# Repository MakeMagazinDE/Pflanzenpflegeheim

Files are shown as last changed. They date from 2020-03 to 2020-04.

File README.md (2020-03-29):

GitHub Logo

Maker Media GmbH
*** 

# Pflanzenpflegeheim
Pflanzenpflegeheim

### Mittels Arduino, Sensoren, Pumpen, Heizung und Lüfter wird dieses Ikea-Gewächshaus zum Luxus-Pflanzenheim.

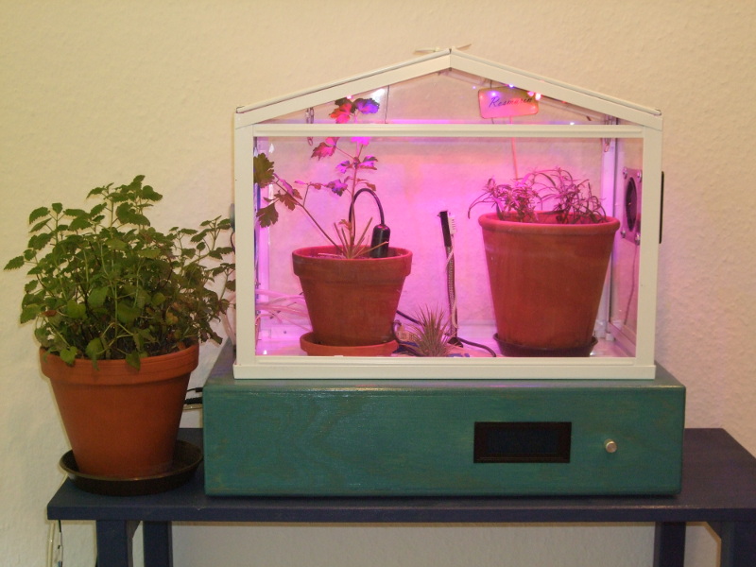
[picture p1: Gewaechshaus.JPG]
 

Den vollständigen Artikel mit der Bauanleitung gibt es in der Make-Ausgabe 2/2020 ab Seite 40 zu lesen.

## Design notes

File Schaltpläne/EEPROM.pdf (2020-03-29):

Adresse | Variable | Byte | Tag bzw. Kanal
0 | Temp an | low | Mo
1 | Temp an | high
2 | Temp an | low | Di
3 | Temp an | high
4 | Temp an | low | Mi
5 | Temp an | high
6 | Temp an | low | Do
7 | Temp an | high
8 | Temp an | low | Fr
9 | Temp an | high
10 | Temp an | low | Sa
11 | Temp an | high
12 | Temp an | low | So
13 | Temp an | high
14 | Temp aus | low | Mo
15 | Temp aus | high
16 | Temp aus | low | Di
17 | Temp aus | high
18 | Temp aus | low | Mi
19 | Temp aus | high
20 | Temp aus | low | Do
21 | Temp aus | high
22 | Temp aus | low | Fr
23 | Temp aus | high
24 | Temp aus | low | Sa
25 | Temp aus | high
26 | Temp aus | low | So
27 | Temp aus | high
28 | Temp aktiv | low | Mo
29 | | high
30 | Temp aktiv | low | Di
31 | | high
32 | Temp aktiv | low | Mi
33 | | high
34 | Temp aktiv | low | Do
35 | | high
36 | Temp aktiv | low | Fr
37 | | high
38 | Temp aktiv | low | Sa
39 | | high
40 | Temp aktiv | low | So
41 | | high
42 | Licht an | low | Mo
43 | Licht an | high
44 | Licht an | low | Di
45 | Licht an | high
46 | Licht an | low | Mi
47 | Licht an | high
48 | Licht an | low | Do
49 | Licht an | high
50 | Licht an | low | Fr
51 | Licht an | high
52 | Licht an | low | Sa
53 | Licht an | high
54 | Licht an | low | So
55 | Licht an | high
56 | Licht aus | low | Mo
57 | Licht aus | high
58 | Licht aus | low | Di
59 | Licht aus | high
60 | Licht aus | low | Mi
61 | Licht aus | high
62 | Licht aus | low | Do
63 | Licht aus | high
64 | Licht aus | low | Fr
65 | Licht aus | high
66 | Licht aus | low | Sa
67 | Licht aus | high
68 | Licht aus | low | So
69 | Licht aus | high
70 | Licht aktiv | low | Mo
71 | | high
72 | Licht aktiv | low | Di
73 | | high
74 | Licht aktiv | low | Mi
75 | | high
76 | Licht aktiv | low | Do
77 | | high
78 | Licht aktiv | low | Fr
79 | | high
80 | Licht aktiv | low | Sa
81 | | high
82 | Licht aktiv | low | So
83 | | high
84 | Pumpe an | low | Mo
85 | Pumpe an | high
86 | Pumpe an | low | Di
87 | Pumpe an | high
88 | Pumpe an | low | Mi
89 | Pumpe an | high
90 | Pumpe an | low | Do
91 | Pumpe an | high
92 | Pumpe an | low | Fr
93 | Pumpe an | high
94 | Pumpe an | low | Sa
95 | Pumpe an | high
96 | Pumpe an | low | So
97 | Pumpe an | high
98 | Pumpe aus | low | Mo
99 | Pumpe aus | high
100 | Pumpe aus | low | Di
101 | Pumpe aus | high
102 | Pumpe aus | low | Mi
103 | Pumpe aus | high
104 | Pumpe aus | low | Do
105 | Pumpe aus | high
106 | Pumpe aus | low | Fr
107 | Pumpe aus | high
108 | Pumpe aus | low | Sa
109 | Pumpe aus | high
110 | Pumpe aus | low | So
111 | Pumpe aus | high
112 | Pumpe aktiv | low | Mo
113 | | high
114 | Pumpe aktiv | low | Di
115 | | high
116 | Pumpe aktiv | low | Mi
117 | | high
118 | Pumpe aktiv | low | Do
119 | | high
120 | Pumpe aktiv | low | Fr
121 | | high
122 | Pumpe aktiv | low | Sa
123 | | high
124 | Pumpe aktiv | low | So
125 | | high
126 | Blende an | low | Mo
127 | Blende an | high
128 | Blende an | low | Di
129 | Blende an | high
130 | Blende an | low | Mi
131 | Blende an | high
132 | Blende an | low | Do
133 | Blende an | high
134 | Blende an | low | Fr
135 | Blende an | high
136 | Blende an | low | Sa
137 | Blende an | high
138 | Blende an | low | So
139 | Blende an | high
140 | Blende aus | low | Mo
141 | Blende aus | high
142 | Blende aus | low | Di
143 | Blende aus | high
144 | Blende aus | low | Mi
145 | Blende aus | high
146 | Blende aus | low | Do
147 | Blende aus | high
148 | Blende aus | low | Fr
149 | Blende aus | high
150 | Blende aus | low | Sa
151 | Blende aus | high
152 | Blende aus | low | So
153 | Blende aus | high
154 | Blende aktiv | low | Mo
155 | | high
156 | Blende aktiv | low | Di
157 | | high
158 | Blende aktiv | low | Mi
159 | | high
160 | Blende aktiv | low | Do
161 | | high
162 | Blende aktiv | low | Fr
163 | | high
164 | Blende aktiv | low | Sa
165 | | high
166 | Blende aktiv | low | So
167 | | high
168 | Bodenfeuchtigkeit | low | 0
169 | | high
170 | Bodenfeuchtigkeit | low | 1
171 | | high
172 | Bodenfeuchtigkeit | low | 2
173 | | high
174 | Bodenfeuchtigkeit | low | 3
175 | | high
176 | Bodenfeuchtigkeit | low | 4
177 | | high
178 | Bodenfeuchtigkeit | low | 5
179 | | high
180 | Bodenfeuchtigkeit | low | 6
181 | | high
182 | Licht | low | -
183 | | high
184 | Luftfeuchtigkeit soll | low | -
185 | | high
186 | Temperatur innen soll | low | -
187 | | high

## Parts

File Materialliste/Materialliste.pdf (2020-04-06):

Für das Gewächshaus

1 IKEA Socker

1 Schrittmotor z.B. 28BYJ-48 (mit Treiber z.B. von Pollin)

1 Silikonschlauch ca. 2 m, 8x2 mm

1 Temperatur/Luftfeuchtigkeitssensor DHT22

1 Pflanzlicht z.B. tronisky LED-Pflanzlampe von Amazon

1 Stück Lochrasterplatte

Elektronikdraht

1-6 Bodenfeuchtigkeitssensor Truebner SMT50

1 SUB-D Stecker 25 polig

1-6 Platinensteckverbinder und Kupplungen 3-polig

4 Kabelbinder

4 Schrauben zur Montage des Lüfters

1 Lüfter 80x80 mm z.B. SUNON MagLev Motor

1 - 2 Heizfolien 12 V, je nach Fläche 1-2 Stück aus dem KFZ-Bedarf

2 Sperrholz Dicke 12 mm, 51 x 28 cm (Oben, Unten)

Für den Sockel

2 Sperrholz Dicke 12 mm, 28 x 9,6 cm (Links, Rechts)

2 Sperrholz Dicke 12 mm, 51 x 9,6 cm (Vorne, Hinten)

1 Arduino Mega

1 Echtzeituhr DS3231

2 Temperatur/Luftfeuchtigkeitssensor DHT22

1 8-fach MOSFET-Treiber Bausatz von Pollin

1 4-fach MOSFET-Treiber Bausatz von Pollin

1-6 12V-Magnetventile CJV23-C12A1 (auf Ebay zu finden)

1 Messingrohr 6 mm Durchmesser, etwa 30 cm

2 Lochrasterkarten

1 LC-Display JOY-IT Display 20x4 Zeichen blau I2C

1 Netzteil 24 V, 5A

2 Step-Down-Wandler LM 2596 (als fertige Platinen verfügbar)

1 Pumpe Reich Tauchpumpe easy 14L/min

1 Sub-D Adapter, 25-polig z.B. von Pollin

2 LED-Treiber Meanwell LDD-500L

2 DC-Hohlstecker mit Kupplung für Heizfolie und Pumpe

1 ULN2003 zusammen mit Schrittmotor z.B. von Pollin

1 Kupplung, zu Netzteil passend

1 Lichtsensor BH 1750

1 5L-Kanister

1 Relais 12 V, mindestens ein Umschalter

1 BD441

1 Widerstand 680 kΩ

2 Widerstände 1 MΩ

1 Widerstand 2,5 kΩ

1 Widerstand 1,5 kΩ

4 Widerstände 10 kΩ

1 Elektrolytkondensator 100 µF

2 Kondensatoren 100 nF

1 Operationsverstärker z.B. LM741

1 Diode 1N4148

Elektronikdraht

diverse Schaltlitzen

diverse Platinensteckverbinder und Kupplungen 2 - 8 polig (optional)

1 Gewindestange M3 zur Befestigung des Arduinos

12 Muttern M3 zur Befestigung des Arduinos

4 Unterlegscheiben M3 zur Befestigung des Arduinos

diverse Platinenschraubverbindungen 2 polig (optional)

1 Drehimpulsgeber mit Taster ALPS - STEC11B

1 Drehknopf zur Welle des Drehimpulsgebers passend

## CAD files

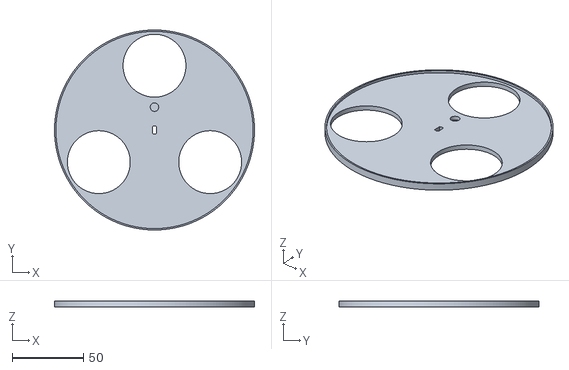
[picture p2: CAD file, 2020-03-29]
3D_Druck/Blende.stl
140.0 x 140.0 x 4.50

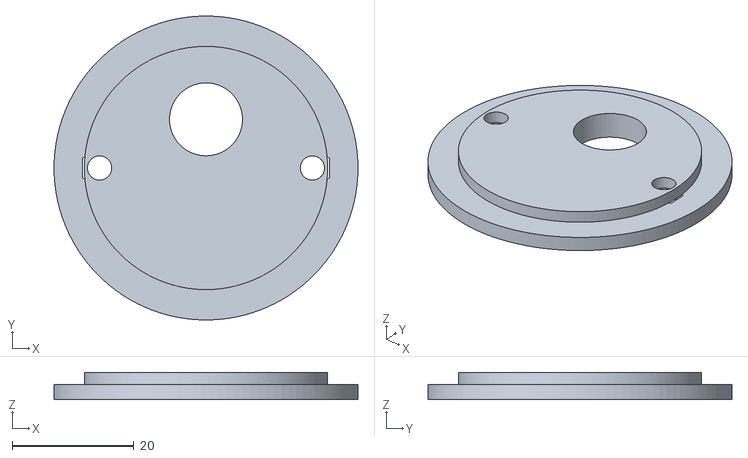
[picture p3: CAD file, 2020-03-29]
3D_Druck/Motorhalter_Blende.stl
50.0 x 50.0 x 4.50

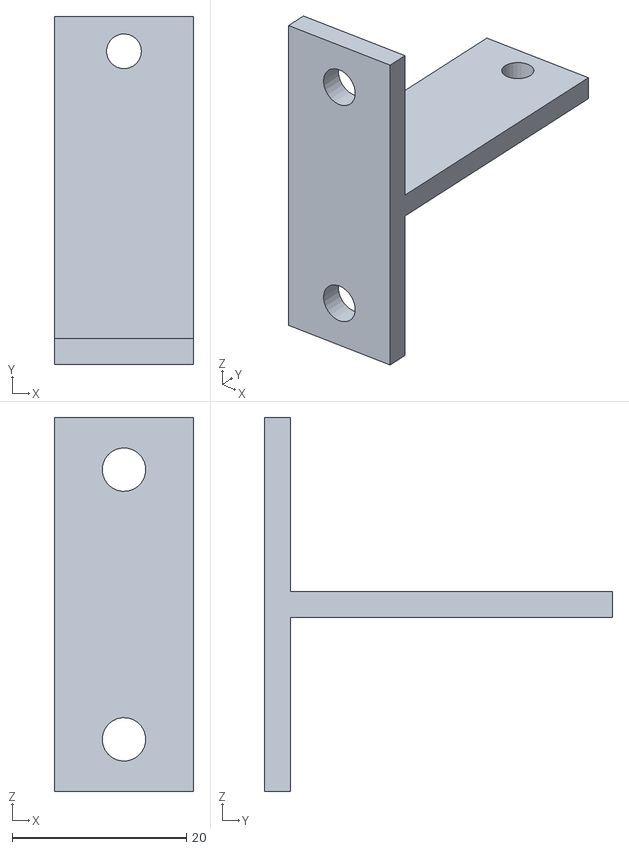
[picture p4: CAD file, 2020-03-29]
3D_Druck/Aufnahme_Tempsensor aussen.stl
16.0 x 40.0 x 43.0

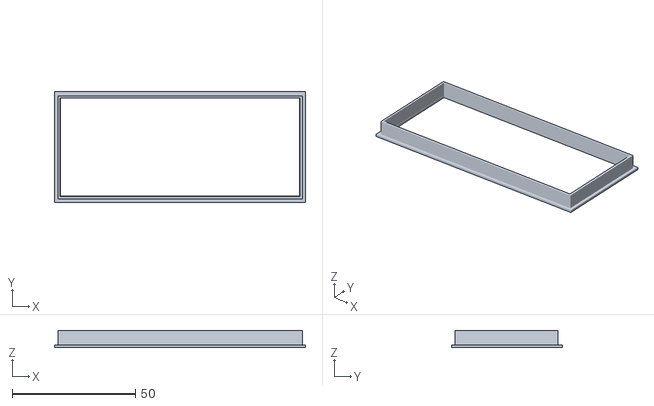
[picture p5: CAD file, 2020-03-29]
3D_Druck/Blende_Display.stl
102.0 x 45.0 x 7.00

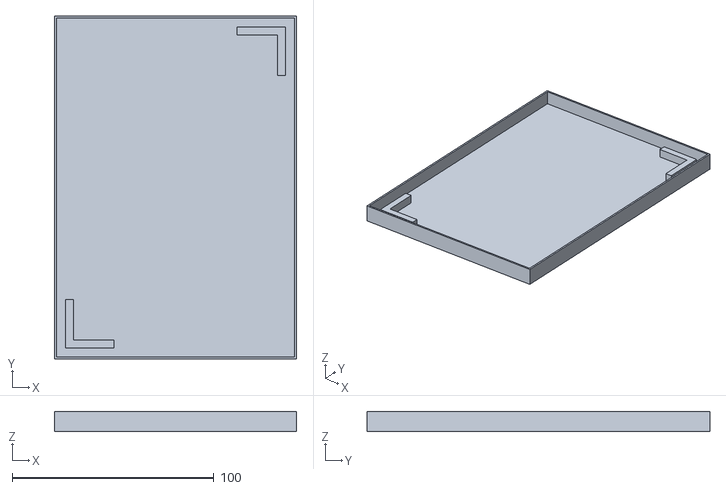
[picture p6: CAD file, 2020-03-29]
3D_Druck/Wanne_rev2.stl
120.0 x 170.0 x 10.0

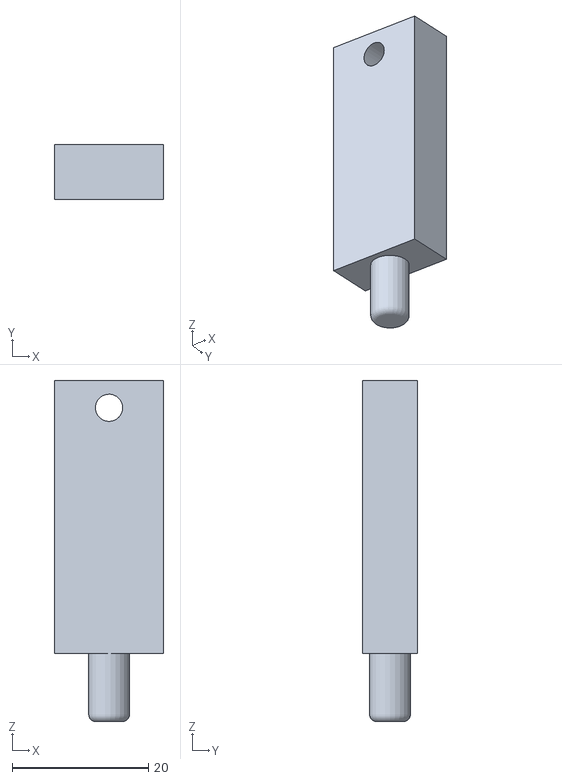
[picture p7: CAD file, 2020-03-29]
3D_Druck/Halterung_DHT22_Innen.stl
16.0 x 8.00 x 50.0

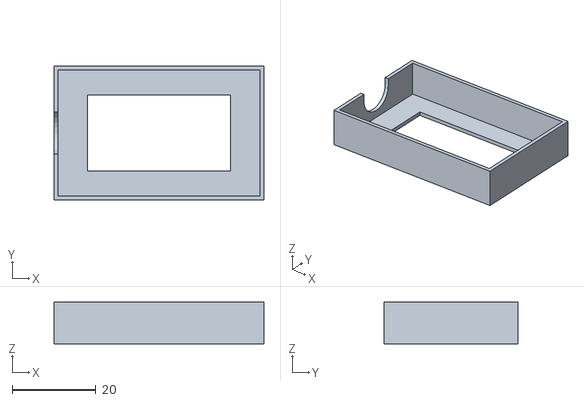
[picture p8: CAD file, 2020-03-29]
3D_Druck/Oberschale_Verteiler_Bodenfeuchtigkeit.stl
50.0 x 32.0 x 10.0

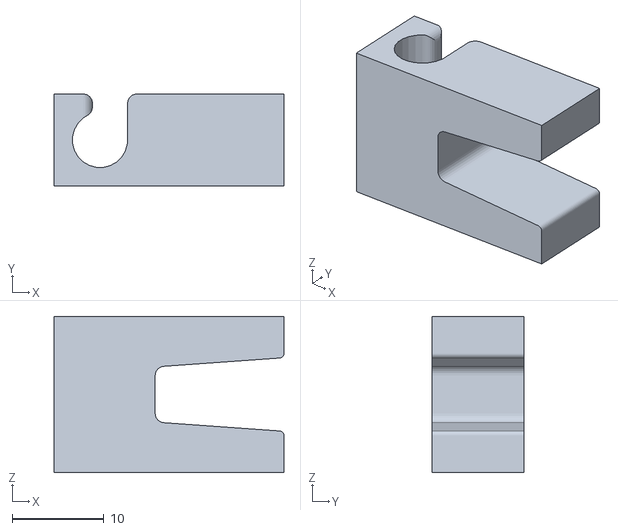
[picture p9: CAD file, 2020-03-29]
3D_Druck/Schlauchclip_fuer_Topf.stl
25.0 x 10.0 x 17.0

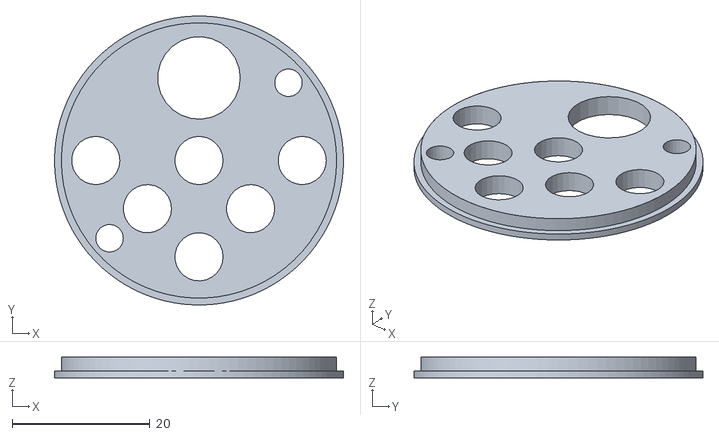
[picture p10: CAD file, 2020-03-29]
3D_Druck/Schlauchdurchfuehrung.stl
42.0 x 42.0 x 3.00

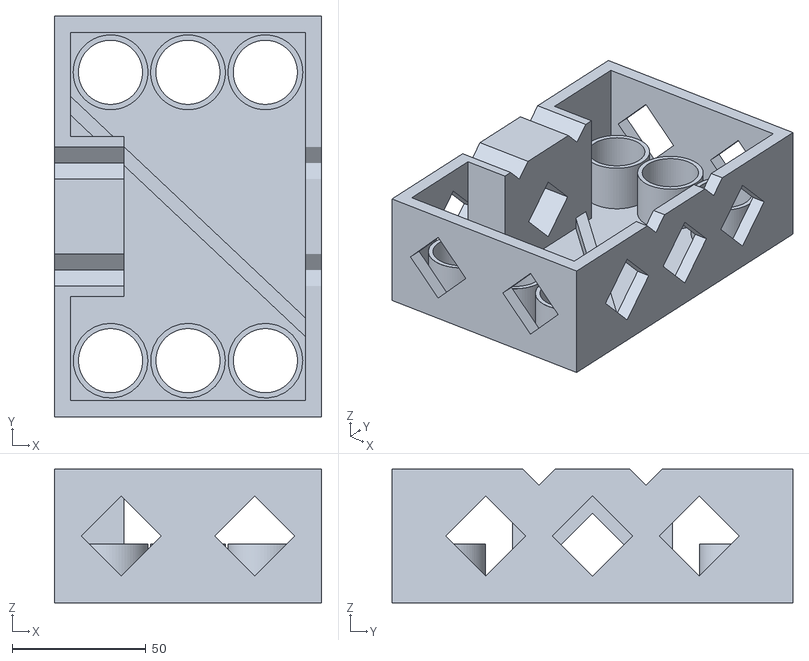
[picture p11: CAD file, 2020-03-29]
3D_Druck/Ventilblock_rev4.stl
100.0 x 150.0 x 50.0

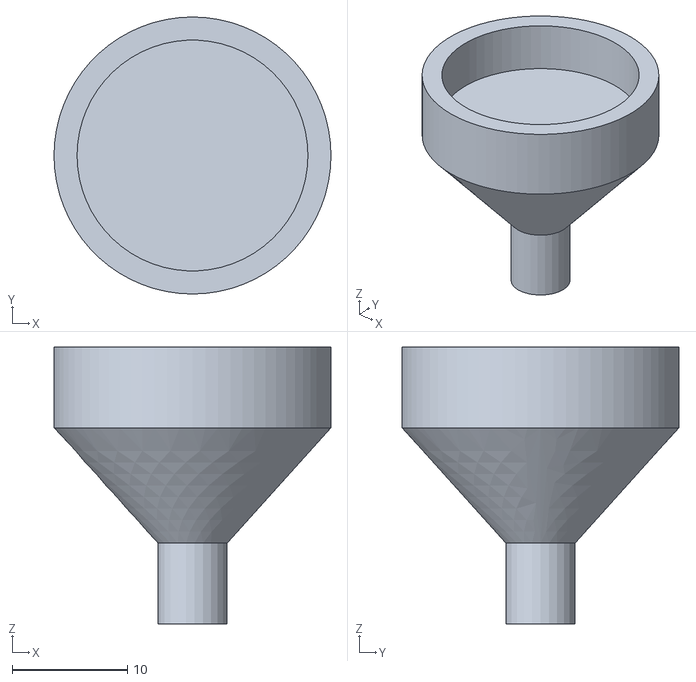
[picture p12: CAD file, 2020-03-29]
3D_Druck/Sockel_Halterung_DHT22_Innen.stl
24.0 x 24.0 x 24.0

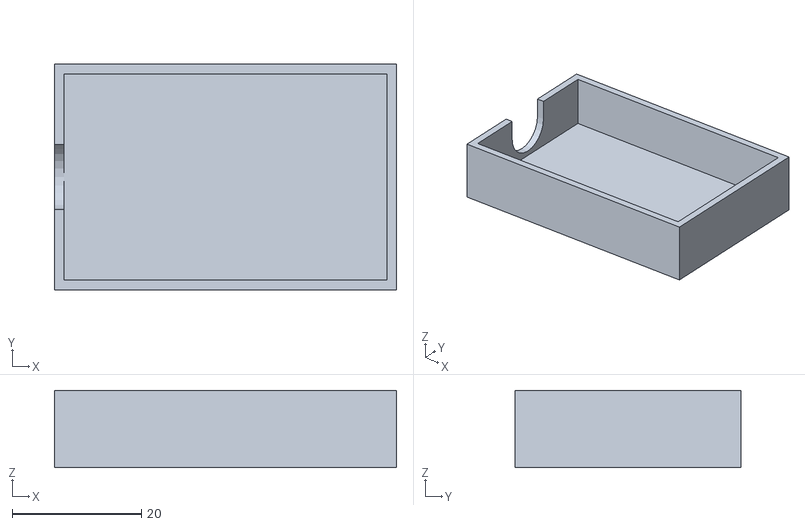
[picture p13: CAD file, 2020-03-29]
3D_Druck/Unterschale_Verteiler_Bodenfeuchtigkeit.stl
53.0 x 35.0 x 12.0

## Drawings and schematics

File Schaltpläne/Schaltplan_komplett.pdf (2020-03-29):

LM2596

IN-

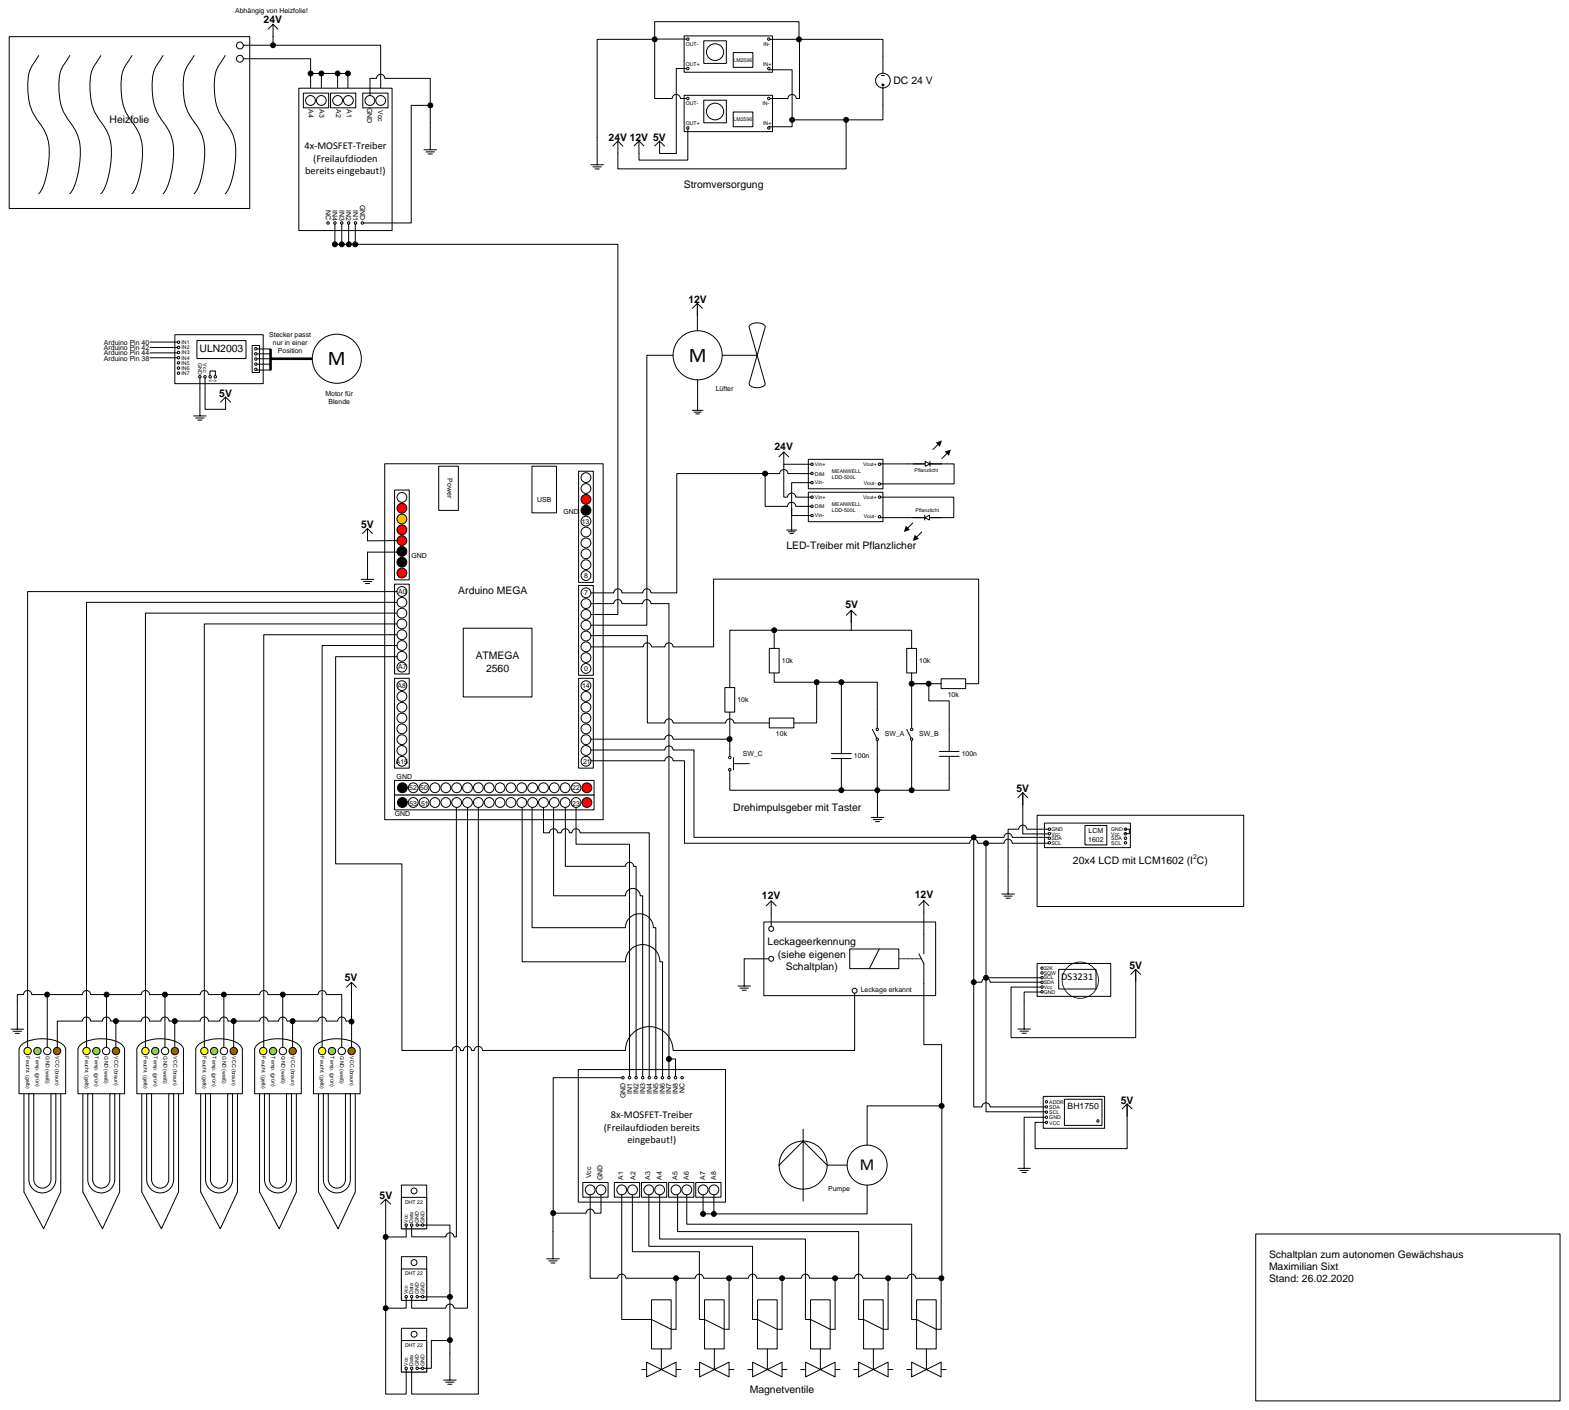
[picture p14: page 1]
Leckageerkennung; (siehe eigenen Schaltplan); Leckage erkannt 12V; Vcc GND; ATMEGA 2560 A0; GND; Power; USB; 20x4 LCD mit LCM1602 (I; C) GND Vcc SDA SCL; GND GND; Lüfter; IN+ OUT-; OUT+; Heizfolie; 24V Abhängig von Heizfolie!; GND Vcc GND; M Pumpe; Vin+; Vin-; DIM; Vout+; Vout- MEANWELL LDD-500L 24V; Pflanzlicht; ULN2003 GND Vcc <->; M Stecker passt nur in einer Position; Magnetventile; Stromversorgung; Arduino MEGA

4x-MOSFET-Treiber (Freilaufdioden bereits eingebaut!)

Motor für Blende 5V Arduino Pin 40 Arduino Pin 42 Arduino Pin 44 Arduino Pin 38

Vout- MEANWELL LDD-500L

LED-Treiber mit Pflanzlicher

Drehimpulsgeber mit Taster

SDA SCL LCM 1602

DS3231 GND Vcc SDA SCL SQW 32K

GND (weiß) VCC (braun) Temp. (grün) Feucht. (gelb)

ADDR SDA SCL GND VCC

8x-MOSFET-Treiber (Freilaufdioden bereits eingebaut!) GND

Vcc Data DHT 22

Schaltplan zum autonomen Gewächshaus Maximilian Sixt Stand: 26.02.2020

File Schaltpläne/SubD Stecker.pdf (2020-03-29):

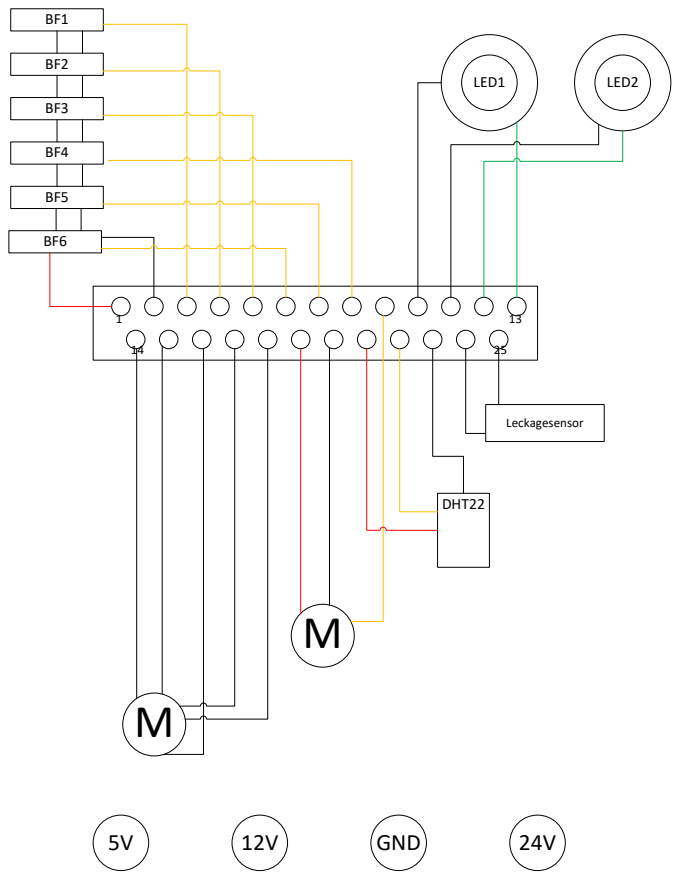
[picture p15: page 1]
DHT22; LED1; LED2; GND; Leckagesensor

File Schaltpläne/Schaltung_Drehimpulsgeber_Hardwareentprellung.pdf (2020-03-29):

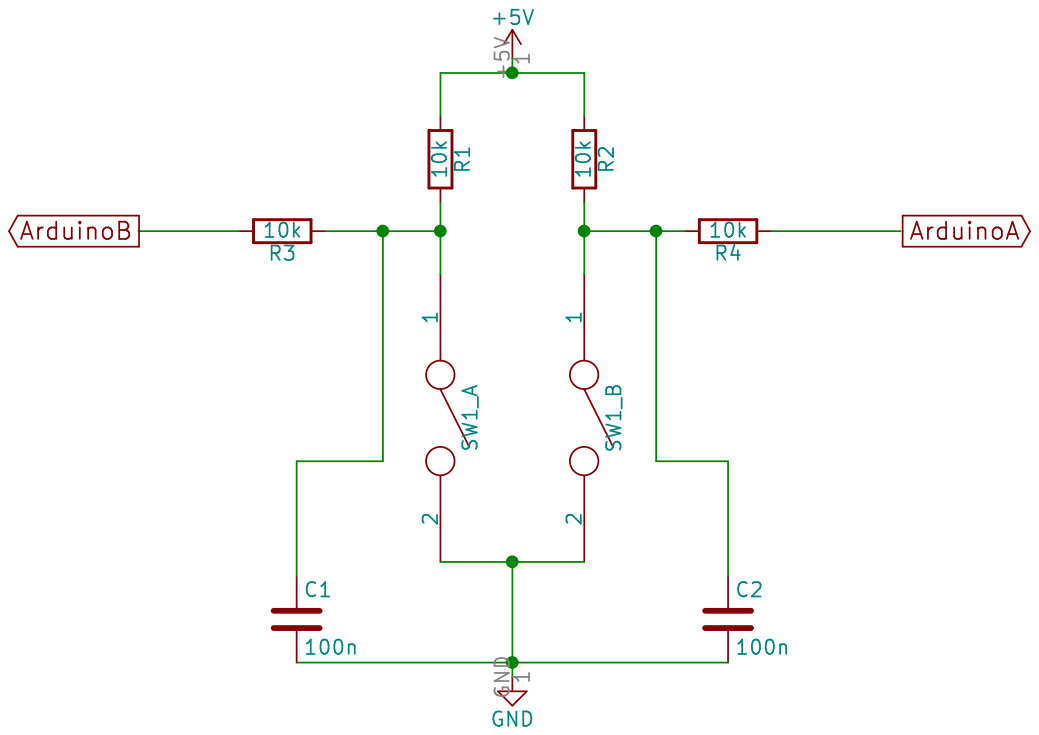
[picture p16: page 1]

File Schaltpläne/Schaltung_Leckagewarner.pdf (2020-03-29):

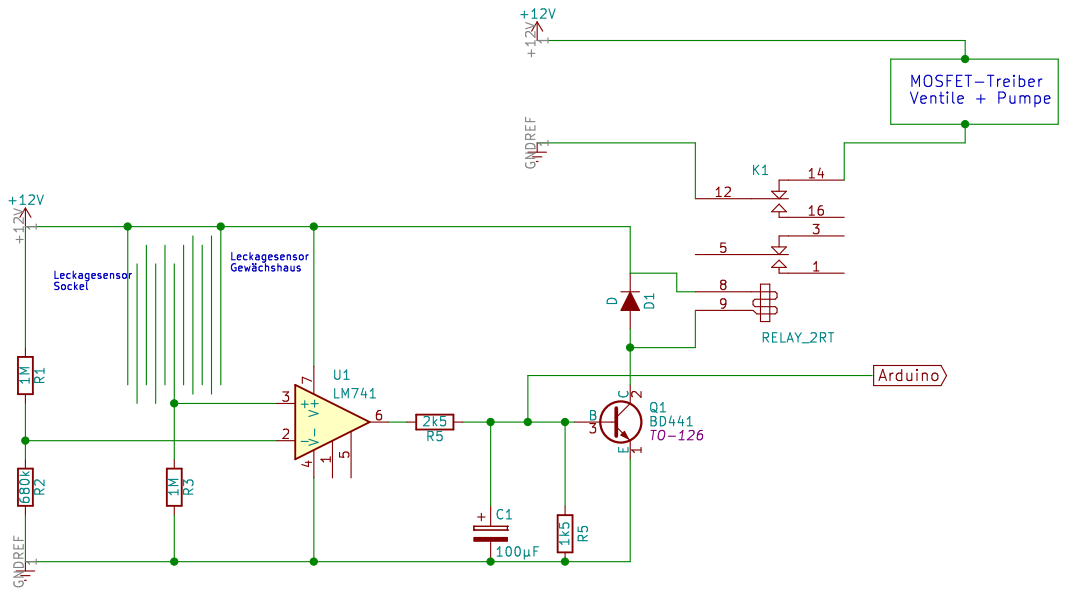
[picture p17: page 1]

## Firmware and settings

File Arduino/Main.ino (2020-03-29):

//Steuerung für Gewächshaus aus Make 2_20
//Dr.-Ing. Maximilian Sixt
//Stand: 12.01.2020

#include <Wire.h>
#include <Time.h>
#include <TimeLib.h>
#include <DS1307RTC.h>
#include <LiquidCrystal_I2C.h>
#include <EEPROM.h>
#include <DHT.h>
#include <math.h>

//Debug Interface
//#define DEBUG//"Schalter" zum aktivieren

#ifdef DEBUG
#define DEBUG_PRINT(x) Serial.print(x)
#define DEBUG_PRINTLN(x) Serial.println(x)
#else
#define DEBUG_PRINT(x)
#define DEBUG_PRINTLN(x)
#endif

//Display
LiquidCrystal_I2C lcd(0x27, 2, 1, 0, 4, 5, 6, 7, 3, POSITIVE);
volatile boolean HintergrundBeleuchtung = false;

//Lichtsensor
int BH1750_Device = 0x23; 

//EEPROM
int address = 0;

//Sonderzeichen
byte TempInnenLCD[8] = { //a
  0b11100,
  0b01000,
  0b01000,
  0b01111,
  0b01010,
  0b00010,
  0b00010,
  0b00111
};

byte TempAussenLCD[8] = { //b
  0b11100,
  0b01000,
  0b01000,
  0b01010,
  0b01101,
  0b00111,
  0b00101,
  0b00101
};

byte FeuchtInnenLCD[8] = { //c
  0b11100,
  0b01000,
  0b11100,
  0b01000,
  0b01111,
  0b00010,
  0b00010,
  0b00111
};

byte FeuchtAussenLCD[8] = { //d
  0b11100,
  0b01000,
  0b11100,
  0b01000,
  0b01010,
  0b00101,
  0b00111,
  0b00101
};

byte BewaesserungLCD[8] = { //e
  0b00100,
  0b11111,
  0b00010,
  0b01000,
  0b00010,
  0b01000,
  0b00010,
  0b01000
};

byte HeizungLCD[8] = { //f
  0b01010,
  0b01110,
  0b01010,
  0b00000,
  0b01010,
  0b10101,
  0b01010,
  0b10101
};
char TiLCD = 0;
char TaLCD = 1;
char FiLCD = 2;
char FaLCD = 3;
char BeLCD = 4;
char HeLCD = 5;

//Temperatur
float TempInnen;
float TempAussen;
float TempElektronik;
float TempSoll = 27;

#define DHTAussenPIN 43
#define DHTInnenPIN 41
#define DHTElektronikPIN 45
#define DHTTYPE DHT22
DHT dhtInnen(DHTInnenPIN, DHTTYPE);
DHT dhtAussen(DHTAussenPIN, DHTTYPE);
DHT dhtElektronik(DHTElektronikPIN, DHTTYPE);

#define HEIZUNG 5

//Menue
#define BUTTON 19 //INT4
#define ENCODERA 2 //INT0
#define ENCODERB 3 //INT1
#define BUZZER 48
volatile boolean Enc_A = false;
volatile boolean Enc_B = false;
volatile boolean pressed = false;
volatile boolean rotating = false;
boolean MenueStatus = false;
volatile boolean A_set = false;
volatile boolean B_set = false;
volatile boolean MenueStart = false;
volatile boolean EncBFlag = false;
volatile boolean EncAFlag = false;

//Luftfeuchtigkeit
float RHInnen;
float RHAussen;
float RHElektronik;
float RHSoll = 55;

//Bodenfeuchtigkeit
int SoilMoisture[6] = {};
bool SoilMoistureStatus[6] = {false, false, false, false, false, false};
int SMUpperThreshold[6] = {0, 0, 0, 0, 0, 0};

#define SM0 A0
#define SM1 A1
#define SM2 A2
#define SM3 A3
#define SM4 A4
#define SM5 A5

#define PUMPE 6
#define LECKAGEPIN A6

#define VENT0 23
#define VENT1 25
#define VENT2 27
#define VENT3 29
#define VENT4 31
#define VENT5 33

//Blende
#define BLENDE1 40
#define BLENDE2 42
#define BLENDE3 44
#define BLENDE4 38

//Luefter
#define FAN 4

//Licht
#define LED 7
int Licht = 50; //0-99

//Datum
const char *monthName[12] = {
  "Jan", "Feb", "Mar", "Apr", "May", "Jun",
  "Jul", "Aug", "Sep", "Oct", "Nov", "Dec"
};
int tag;
String Tage[] = {"So", "Mo", "Di", "Mi", "Do", "Fr", "Sa"};
tmElements_t tm;

//Zeitprogramme: So, Mo, Di, Mi, Do, Fr, Sa
int LichtAn[7] = {540, 420, 420, 420, 420, 420, 540};
int LichtAus[7] = {1140, 1140, 1140, 1140, 1140, 1140, 1140};
bool LichtSteuerung[7] = {true, true, true, true, true, true, true};
int PumpeAn[7] = {540, 390, 390, 390, 390, 390, 540};
int PumpeAus[7] = {1200, 1200, 1200, 1200, 1200, 1200, 1200};
bool Bewaesserung[7] = {true, true, true, true, true, true, true};
int TempAn[7] = {360, 360, 360, 360, 360, 360, 360};
int TempAus[7] = {1140, 1140, 1140, 1140, 1140, 1140, 1140};
bool TempRegelung[7] = {true, true, true, true, true, true, true};
int BlendeAn[7] = {540, 420, 420, 420, 420, 420, 540}; //=Fan
int BlendeAus[7] = {1200, 1200, 1200, 1200, 1200, 1200, 1200};; //=Fan
bool RHRegelung[7] = {true, true, true, true, true, true, true};

void Button(void);
void doEncoderA(void);
void doEncoderB(void);

float Verbrauch[4] = {0, 0, 0, 0}; //Stromverbrauch aktuell, letzte 24h, letzte 48h, letzte 72h

void setup(void) {
  pinMode(BLENDE1, OUTPUT);
  pinMode(BLENDE2, OUTPUT);
  pinMode(BLENDE3, OUTPUT);
  pinMode(BLENDE4, OUTPUT);
  pinMode(VENT0, OUTPUT);
  pinMode(VENT1, OUTPUT);
  pinMode(VENT2, OUTPUT);
  pinMode(VENT3, OUTPUT);
  pinMode(VENT4, OUTPUT);
  pinMode(VENT5, OUTPUT);
  pinMode(BUTTON, INPUT);
  pinMode(ENCODERA, INPUT);
  pinMode(ENCODERB, INPUT);
  pinMode(LECKAGEPIN, INPUT);
  digitalWrite(BLENDE1, LOW);
  digitalWrite(BLENDE2, LOW);
  digitalWrite(BLENDE3, LOW);
  digitalWrite(BLENDE4, LOW);
  digitalWrite(VENT0, LOW);
  digitalWrite(VENT1, LOW);
  digitalWrite(VENT2, LOW);
  digitalWrite(VENT3, LOW);
  digitalWrite(VENT4, LOW);
  digitalWrite(VENT5, LOW);
  pinMode(SM0, INPUT);
  pinMode(SM1, INPUT);
  pinMode(SM2, INPUT);
  pinMode(SM3, INPUT);
  pinMode(SM4, INPUT);
  pinMode(SM5, INPUT);
  pinMode(FAN, OUTPUT);
  pinMode(LED, OUTPUT);
  pinMode(PUMPE, OUTPUT);
  pinMode(HEIZUNG, OUTPUT);
  digitalWrite(FAN, LOW);
  analogWrite(LED, 0);
  digitalWrite(PUMPE, LOW);
  analogWrite(HEIZUNG, 0);
  TCCR3B = (TCCR3B & 0xF8) | 0x05 ; //PWM Frequenz von Pin 5 (Heizung niedirg)
  TCCR4B = (TCCR4B & 0xF8) | 0x01 ; //PWM Frequenz von Pin 7 (LED hoch)
  attachInterrupt(digitalPinToInterrupt(BUTTON), Button, HIGH);
  attachInterrupt(digitalPinToInterrupt(ENCODERA), doEncoderA, CHANGE);
  attachInterrupt(digitalPinToInterrupt(ENCODERB), doEncoderB, CHANGE);
  Wire.beginTransmission (BH1750_Device);
  Wire.write(0x10); // Set resolution to 1 Lux
  Wire.endTransmission ();

  lcd.begin(20, 4);
  lcd.createChar(TiLCD, TempInnenLCD);
  lcd.createChar(TaLCD, TempAussenLCD);
  lcd.createChar(FiLCD, FeuchtInnenLCD);
  lcd.createChar(FaLCD, FeuchtAussenLCD);
  lcd.createChar(BeLCD, BewaesserungLCD);
  lcd.createChar(HeLCD, HeizungLCD);
  dhtInnen.begin();
  dhtAussen.begin();
  dhtElektronik.begin();
  Serial.begin(9600);
  setSyncProvider(RTC.get);
}//setup

void save(int wert) {
  //Funktion zum Speichern in den EEPROM. Wird aufgerufen von "Speichern". 
  //Daten werden in zwei Bytes zerlegt, da das Programm die An- bzw. Abschaltzeiten nur als Minuten (max. 24*60 = 1440) kennt und diese in zwei Bytes gespeichert werden müssen. 
  //Daten die nur ein Byte belegen werden im low-Byte gespeichert um Code einfach zu gestalten.
  byte high;
  byte low;
  low = wert % 255;
  high = (wert - low) / 255;
  EEPROM.write(address, low);
  address = address + 1;
  EEPROM.write(address, high);
  address = address + 1;
}//save

int restore(void) {
	//Lädt die Werte des Menüs aus dem EEPROM. Wird aufgerufen von "Wiederherstellen".
  int high;
  int low;
  int value;
  byte EEPROMhigh;
  byte EEPROMlow;
  low = EEPROM.read(address);
  address = address + 1;
  high = 255 * EEPROM.read(address);
  address = address + 1;
  value = high + low;
  return value;
}//restore

void Speichern(void) {
	//Speichert die Menüeinträge in den EEPROM, wird beim Beenden des Menüs automatisch aufgerufen, sie Datei EEPROM.pdf
  address = 0;
  //Temp
  for (int i = 0; i <= 6; i++) {
    save(TempAn[i]);
  }
  for (int i = 0; i <= 6; i++) {
    save(TempAus[i]);
  }
  for (int i = 0; i <= 6; i++) {
    save(TempRegelung[i]);
  }
  //Licht
  for (int i = 0; i <= 6; i++) {
    save(LichtAn[i]);
  }
  for (int i = 0; i <= 6; i++) {
    save(LichtAus[i]);
  }
  for (int i = 0; i <= 6; i++) {
    save(LichtSteuerung[i]);
  }
  //Bewaesserung
  for (int i = 0; i <= 6; i++) {
    save(PumpeAn[i]);
  }
  for (int i = 0; i <= 6; i++) {
    save(PumpeAus[i]);
  }
  for (int i = 0; i <= 6; i++) {
    save(Bewaesserung[i]);
  }
  //Blende
  for (int i = 0; i <= 6; i++) {
    save(BlendeAn[i]);
  }
  for (int i = 0; i <= 6; i++) {
    save(BlendeAus[i]);
  }
  for (int i = 0; i <= 6; i++) {
    save(RHRegelung[i]);
  }
  //SM Voreinstellungen
  for (int i = 0; i <= 5; i++) {
    save(SMUpperThreshold[i]);
  }
  save(Licht);
  save(RHSoll);
  save(TempSoll);
}

void Wiederherstellen(void) {
	//Startet das Wiederherstellen der Menüeinträge, siehe auch Datei EEPROM.pdf
  address = 0;
  //Temp
  for (int i = 0; i <= 6; i++) {
    (TempAn[i]) = restore();
  }
  for (int i = 0; i <= 6; i++) {
    (TempAus[i]) = restore();
  }
  for (int i = 0; i <= 6; i++) {
    (TempRegelung[i]) = restore();
  }
  //Licht
  for (int i = 0; i <= 6; i++) {
    (LichtAn[i]) = restore();
  }
  for (int i = 0; i <= 6; i++) {
    (LichtAus[i]) = restore();
  }
  for (int i = 0; i <= 6; i++) {
    (LichtSteuerung[i]) = restore();
  }
  //Bewaesserung
  for (int i = 0; i <= 6; i++) {
    (PumpeAn[i]) = restore();
  }
  for (int i = 0; i <= 6; i++) {
    (PumpeAus[i]) = restore();
  }
  for (int i = 0; i <= 6; i++) {
    (Bewaesserung[i]) = restore();
  }
  //Blende
  for (int i = 0; i <= 6; i++) {
    (BlendeAn[i]) = restore();
  }
  for (int i = 0; i <= 6; i++) {
    (BlendeAus[i]) = restore();
  }
  for (int i = 0; i <= 6; i++) {
    (RHRegelung[i]) = restore();
  }
  //SM Voreinstellungen
  for (int i = 0; i <= 5; i++) {
    (SMUpperThreshold[i]) = restore();
  }
  Licht = restore();
  RHSoll = restore();
  TempSoll = restore();
}

void Menue(void) {
	//Menü zur Einstellung der Parameter des Gewächshauses
  String HauptMenueEntry[] = {"Info", "Temperatur>", "Feuchtigkeit>", "Bewaesserung>", "Blende>", "Licht>", "Programme>", "System>"};
  String TempMenueEntry[] = {"Menue", "Sollwert:", "Istwert:"};
  String FeuchtMenueEntry[] = {"Menue", "Sollwert:", "Istwert:"};
  String BewaesserungMenueEntry[] = {"Menue", "Sollwert1:", "Istwert1:", "Kanal1 ", "Sollwert2:", "Istwert2:", "Kanal2 ", "Sollwert3:", "Istwert3:", "Kanal3 ", "Sollwert4:", "Istwert4:", "Kanal4 ", "Sollwert5:", "Istwert5:", "Kanal5 ", "Sollwert6:", "Istwert6:", "Kanal6 "};
  String LichtMenueEntry[] = {"Menue", "Leistung: "};
  String BlendeMenueEntry[] = {"Menue", "Home>"};
  String ProgrammeMenueEntry[] = {"Menue", "Sonntag>", "Montag>", "Dienstag>", "Mittwoch>", "Donnerstag>", "Freitag>", "Samstag>" , "Wiederherstellen"};
  String TagMenueEntry[] = {"Luefter an : ", "Luefter aus: ", "Luefter: ", "Pumpe an : ", "Pumpe aus: ", "Pumpe: ", "Licht an : ", "Licht aus: ", "Licht: ", "Heizung an : ", "Heizung aus: ", "Heizung: "};
  String SystemMenueEntry[] = {"Menue", "TempElektronik:", "Feucht.Elek:", "Uhrzeit ", "Verbr. akt: ", "Verbr. 24h: ", "Verbr. 48h: ", "Verbr. 72h: "};
  int MAXHAUPTMENUE = 7;
  int MAXTEMPMENUE = 1;
  int MAXFEUCHTMENUE = 1;
  int MAXBEWAESSERUNGMENUE = 12;
  int MAXBLENDEMENUE = 1;
  int MAXLICHTMENUE = 1;
  int MAXPROGRAMMEMENUE = 8;
  int MAXTAGMENUE = 12; //Eigentlich 11, einer geht aber für den Wochentag drauf!
  int MAXSYSTEMMENUE = 1;
  int MAXEBENE = 30;
  int counter[MAXEBENE] = {0};
  int MAXCOUNTER[] = {MAXHAUPTMENUE, MAXTEMPMENUE, MAXFEUCHTMENUE, MAXBEWAESSERUNGMENUE, MAXBLENDEMENUE, MAXLICHTMENUE, MAXPROGRAMMEMENUE, MAXSYSTEMMENUE};
  int counterWert = 0;
  int Ebene = 0;
  int counter60 = 0; //Montag
  int counterStunde = tm.Hour;
  int counterMinute = tm.Minute;;
  int LayerIndex = 0;
  int TagIndex = 0;

  MenueStatus = true;
  lcd.backlight();

  digitalWrite(PUMPE, LOW);
  digitalWrite(VENT0, LOW);
  digitalWrite(VENT1, LOW);
  digitalWrite(VENT2, LOW);
  digitalWrite(VENT3, LOW);
  digitalWrite(VENT4, LOW);
  digitalWrite(VENT5, LOW);
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
void loop(void) { //Eigentliches Hauptprogramm
  int thetime; //Aktuelle Uhrzeit als Produkt von Stunde * Minute.
  unsigned int Lux; //Lichtstärke
  static long Ttast = 10; //[Sekunden]. Zeit, die das Programm wartet bis es von vorne beginnt, wird ebenso als Tastzeit für den PID-Regler benötigt.
  static float e = 0; //Regelabweichung
  static float esum = 0; //I-Glied
  static float ealt = 0; //D-Glied
  static int Ki = 6; //Integralanteil
  static int Kp = 180; //Proportionalanteil
  static int Kd = 2000; //Differentialanteil
  static float y; //Stellgröße
  float HeizungAnzeige = 0; //LCD-Anzeige der Heizleistung (0-99)
  static float LichtPWM; //PWM für LEDs
  static bool busy = false; //Variable dient dazu im LCD den gerade bewässerten Kanal anzuzeigen
  static unsigned long LCDtime = 0;
  static bool Leckage = false;
  static bool leer = false; //Hilfsvariable falls Füllstandsüberwachung des Kanisters implementiert wird. Wird derzeit nicht geändert.
  static bool aktualisieren = true; //Variable zum Reset des Verbrauchszählers.
  static unsigned long Timer1 = 0; //Startzeit des Hauptprogramms
  static unsigned long Timer2 = 0; //Endzeit des Hauptprogramms
  boolean Vent0 = false;
  boolean Vent1 = false;
  boolean Vent2 = false;
  boolean Vent3 = false;
  boolean Vent4 = false;
  boolean Vent5 = false;
  long Mittelwert = 0; //Mittelwert der Bodenfeuchtigkeiten pro Sensor
  int MAX = 5; //Anzahl der Messwerte der Bodenfeuchtigkeitssensoren
  float RHInnen_abs; //Absolute Luftfeuchtigkeit innen
  float RHAussen_abs; //Absolute Luftfeuchtigkeit außen
  static int DiffZeit = 60; //Zeitdifferenz die die Pumpe pro Kanal wartet, bis sie wieder aktiv wird.
  static int SoilMoistureTimer[6] = {0, 0, 0, 0, 0, 0}; //Speichert den Zeitpunkt an dem bewässert wurde.
  static float Fakt_Verbrauch[4] = {0.000519216, 0.00019343, 0.002933333, 0.0008}; //Faktoren zur Berechnung des Stromverbrauchs: Heizung, Licht, Konstant, Lüfter, siehe auch Datei Verbrauch.pdf
  
  Timer1 = millis(); //Starten des Timers um Laufzeit des Programms zu ermitteln (wichtig für PID).

  RTC.read(tm);
  tag = weekday() - 1;
  thetime = tm.Hour * 60 + tm.Minute;
  DEBUG_PRINTLN("Tag:\t" + String(tag));
  DEBUG_PRINTLN("thetime:\t" + String(thetime));
  //Leckagesensor auslesen
  if (digitalRead(LECKAGEPIN) == LOW) {
    Leckage = true;
    alarm("Leckage!");
    DEBUG_PRINTLN("Leckage!");
  }
  else {
    Leckage = false;
  }
  //Luftfeuchtigkeiten auslesen
  RHInnen = dhtInnen.readHumidity();
  RHInnen = int(RHInnen);
  if (RHInnen == 0 || isnan(RHInnen)) {
    alarm("Feucht. innen Sensor");
    RHInnen = 50;
  }
  RHAussen = dhtAussen.readHumidity();
  RHAussen = int(RHAussen);
  if (RHAussen == 0 || isnan(RHAussen)) {
    alarm("Feucht. aussen Sensor");
    RHAussen = 40;
  }
  RHElektronik = dhtElektronik.readHumidity();
  RHElektronik = int(RHElektronik);
  if (RHElektronik == 0 || isnan(RHElektronik)) {
    alarm("Feucht. Elektronik Sensor");
    RHElektronik = 40;
  }
  if (RHElektronik > 60) {
    Leckage = true;
  }

  DEBUG_PRINTLN("Feuchtigkeit innen:\t" + String(RHInnen));
  DEBUG_PRINTLN("Feuchtigkeit aussen:\t" + String(RHAussen));
  DEBUG_PRINTLN("Feuchtigkeit Elektronik:\t" + String(RHElektronik));
  DEBUG_PRINTLN("Feuchtigkeit Sollwert:\t" + String(RHSoll));
  
  //Temperaturen auslesen
  TempInnen = dhtInnen.readTemperature();
  if (isnan(TempInnen)) {
    alarm("Temp innen Sensor");
    TempInnen = 25.0;
  }
  TempAussen = dhtAussen.readTemperature();
  if (isnan(TempAussen)) {
    alarm("Temp aussen Sensor");
    TempAussen = 22.0;
  }
  TempElektronik = dhtElektronik.readTemperature();
  if (isnan(TempElektronik)) {
    alarm("Temp Elektronik Sensor");
    TempElektronik = 30.0;
  }

  //Relative (gemessene) Luftfeuchtigkeiten in absolute Luftfeuchtigkeiten umrechnen
  RHInnen_abs = (6.112 * exp((17.67 * TempInnen) / (TempInnen + 243.5)) * RHInnen * 2.1674) / (273.15 + TempInnen);
  RHAussen_abs = (6.112 * exp((17.67 * TempAussen) / (TempAussen + 243.5)) * RHAussen * 2.1674) / (273.15 + TempAussen);

  DEBUG_PRINTLN("Absolute Feuchtigkeit innen (g/m³):\t" + String(RHInnen_abs));
  DEBUG_PRINTLN("Absolute Feuchtigkeit aussen (g/m³):\t" + String(RHAussen_abs));
  DEBUG_PRINTLN("Temperatur innen:\t" + String(TempInnen));
  DEBUG_PRINTLN("Temperatur aussen:\t" + String(TempAussen));
  DEBUG_PRINTLN("Temperatur Elektronik:\t" + String(TempElektronik));
  DEBUG_PRINTLN("Temperatur Sollwert:\t" + String(TempSoll));

  //Temperaturregelung
  if (TempRegelung[tag] == true) {
    if ((thetime <= TempAus[tag] && thetime >= TempAn[tag])) {
      if (TempElektronik < 60) {//Falls die Temperatur der Elektronik größer als 60°C ist (willkürlich geschätzter Wert) dann stimmt irgendwas so gar nicht, nicht heizen und Warnung über LCD ausgeben.
        e = TempSoll - TempInnen;
        DEBUG_PRINTLN("Regelabweichung: " + String(e));
        if (e >= 1.0) { //Regelabweichung sehr groß (z.B. durch Temperaturänderung im Menü, also heizen was das Zeug hält.
          DEBUG_PRINTLN("Regelabweichung > 1, Reiner P-Regler");
          analogWrite(HEIZUNG, 255);
          HeizungAnzeige = 99;
        }
        else {
          y = Kp * e + Ki * Ttast * esum + Kd / Ttast * (e - ealt); //Eigentlicher PID-Regler
          ealt = e;
          DEBUG_PRINTLN("Stellgröße: " + String(y));
          DEBUG_PRINTLN("Esum: " + String(esum));
          if (y >= 0 && y < 255) { //Anti-Windup
            esum = esum + e;
            DEBUG_PRINTLN("esum update");
          }
          if (y < 0) {//Begrenzung PWM-Signal
            y = 0;
            DEBUG_PRINTLN("Y = 0");
          }
          if (y >= 255) {//Begrenzung PWM-Signal
            y = 255;
            DEBUG_PRINTLN("Y = 255");
          }
          analogWrite(HEIZUNG, int(y));
          HeizungAnzeige = y / 2.57; //Umrechnung von 0-255 (PWM-Signal) auf Prozent für LCD
        }//else (PID)
      }//if Temp Elektronik
      else {
        alarm("Temp. Elektronik pruefen");
      }//else
    }//if thetime <= TempAn usw.
    else {
      analogWrite(HEIZUNG, 0);
      DEBUG_PRINTLN("Temp aus");
    }
  }//if thetime <= TempAn usw.
  else {
    analogWrite(HEIZUNG, 0);
    DEBUG_PRINTLN("Temp aus");
  }

  //Luftfeuchtigkeitsregelung
  if (RHRegelung[tag] == true) {
    if (thetime <= BlendeAus[tag] && thetime >= BlendeAn[tag]) {
      if ((RHInnen > RHSoll) && (RHInnen_abs > RHAussen_abs)){
        if (RHInnen - RHSoll > 10) {
          Blende(10); //Maximal offen
          DEBUG_PRINTLN("Blende auf + Lüfter, zu feucht");
          digitalWrite(FAN, HIGH);
        }
        if (RHInnen - RHSoll  <= 10) {
          Blende(RHInnen - RHSoll); //Blende partiell öffnen
          digitalWrite(FAN, HIGH);
          DEBUG_PRINTLN("Blende teilweise + Lüfter, zu feucht");
        }
        if (RHInnen <= RHSoll) {
          Blende(0);
          digitalWrite(FAN, LOW);
          DEBUG_PRINTLN("Blende zu, zu trocken");
        }
      }
      else {
        digitalWrite(FAN, LOW);
        Blende(0);
      }
    }
    else {
      digitalWrite(FAN, LOW);
      Blende(0);
    }

  }//if RHRegelung
  else {
    digitalWrite(FAN, LOW);
    Blende(0);
  }

  //Lichtsteuerung
  if (LichtSteuerung[tag] == true) {
    if (thetime <= LichtAus[tag] && thetime >= LichtAn[tag]) {
      Lux = BH1750_Read();
      DEBUG_PRINTLN("Lux: " + String(Lux));
      if (Lux < 2000) {//LEDs werden erst angeschaltet, wenn es dunkel ist (2000 ist geschätzter Wert)
        LichtPWM = 255 * Licht * (1 - (Lux*0.0005)) / 99 ; //Formel für PWM-Signal in Abhängigkeit der aktuellen Helligkeit
        analogWrite(LED, int(LichtPWM));
        DEBUG_PRINTLN("LichtPWM" + String(LichtPWM));
      }
      else{
        LichtPWM = 0;
        analogWrite(LED, 0);
      }
    }
    else {
      DEBUG_PRINTLN("Licht aus");
      analogWrite(LED, 0);
    }
  }
  else {
    analogWrite(LED, 0);
  }

  //Bodenfeuchtigkeit auslesen
  pinMode(SM0, INPUT_PULLUP);
  pinMode(SM1, INPUT_PULLUP);
  pinMode(SM2, INPUT_PULLUP);
  pinMode(SM3, INPUT_PULLUP);
  pinMode(SM4, INPUT_PULLUP);
  pinMode(SM5, INPUT_PULLUP);
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
